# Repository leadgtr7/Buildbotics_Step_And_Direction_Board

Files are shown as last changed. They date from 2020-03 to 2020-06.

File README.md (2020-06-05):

Buildbotics Step and Direction Breakout and Level Shifter
======

### Intro
This is a step and direction breakout board and level shifter for the awesome Buildbotics CNC controller (https://buildbotics.com/ and https://github.com/buildbotics).

This board has been tested with the CL57Y closed loop stepper driver (https://www.omc-stepperonline.com/closed-loop-stepper-driver/y-series-closed-loop-stepper-driver-0-7-0a-24-50vdc-for-nema-17-23-24-stepper-motor.html).

I suspect that it will work with most drivers that have a minimum pulse width of 2.5uS even though the buildbotics control has a pulse width of 2 uS it just seems to work.

This board involves some small surface mount components (SOIC-8) so soldering skills are a must!

### You will need the following parts for the board

| Qty	| P/N	| Digikey Link |
| ---- | ---- | ---- |
|4x	|SN75451BDR	|https://www.digikey.com/product-detail/en/texas-instruments/SN75451BDR/296-14960-1-ND/562591|
|12x	|Generic Header Pins 2.54mm spacing	|https://www.amazon.com/MCIGICM-Header-2-45mm-Arduino-Connector/dp/B07PKKY8BX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|
|2x	|PCB-MB-01|https://www.digikey.com/product-detail/en/essentra-components/PCB-MB-01/RPC1760-ND/393158|
|4x |3 pin plugable terminal blocks 3.81mm spacing |https://www.amazon.com/gp/product/B07SVNGBZ7/ref=ppx_yo_dt_b_search_asin_title?ie=UTF8&psc=1|
|4x |0805 0.1uF Cap|https://www.digikey.com/product-detail/en/stackpole-electronics-inc/CML0805Y5V104ZT50V/738-CML0805Y5V104ZT50VCT-ND/10660252|

### Buildbotics PCB Modifications
You will need to solder in headers to the bbctrl board to make step and direction available as well as a 2 pin header with 5v and Ground. This will vary based on the version of your control board. You can find the schematics for the differnt revs here (https://github.com/buildbotics/bbctrl-pcb/tree/master/doc). For my controller (rev 8) you can see below for the locations.

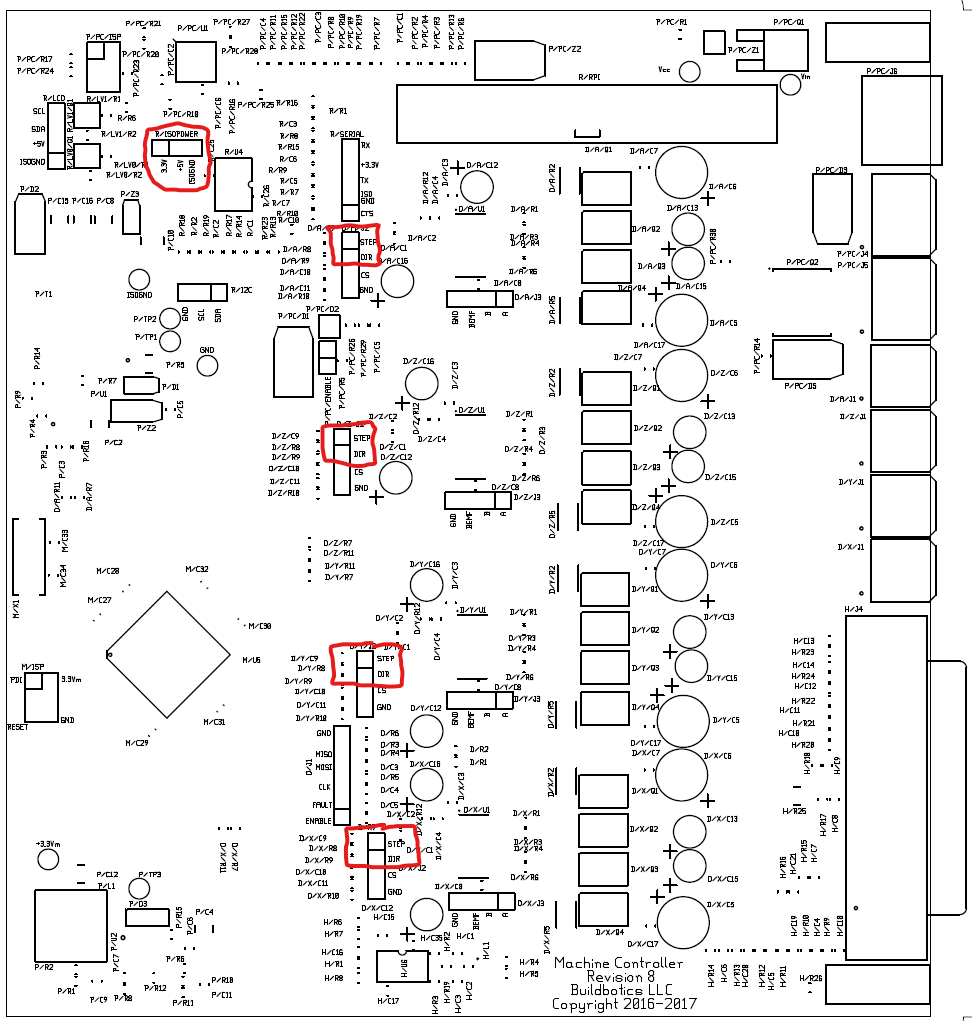
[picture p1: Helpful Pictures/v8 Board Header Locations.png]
v8 Header Locations


You will also need to make a harness to connect the 10 pins on the bbctrl to the step and direction board. If you aren't comfortable crimping your own harness you could use something like this (https://www.amazon.com/EDGELEC-Breadboard-Optional-Assorted-Multicolored/dp/B07GCY6CH7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) for your harness.

### PCB Assembly
The image below shows the location of all the headers and how to solder the ICs to the board. Each of the 3 pin connectors provides the step and direction output and the 4 sets of 2 pins are wired to the buildbotics pcb header you need to install. Remeber that as you plug in the cable on the back that they will be reversed on the front so pay attention to that.

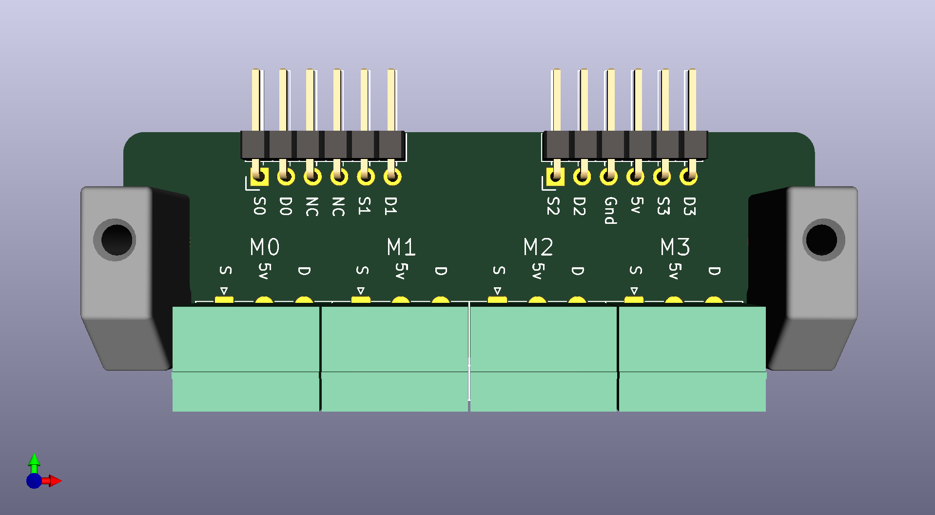
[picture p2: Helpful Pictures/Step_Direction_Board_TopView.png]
Front PCB


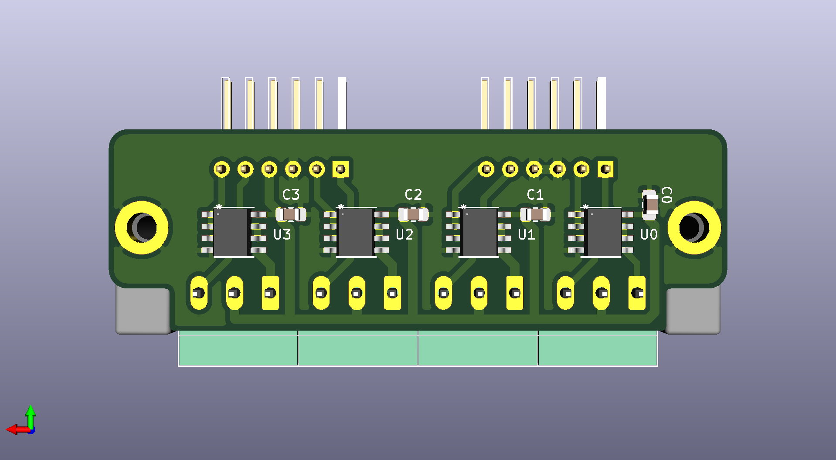
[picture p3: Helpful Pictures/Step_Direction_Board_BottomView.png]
Back PCB


note the direction of pin 1 of the IC's

### New Back Panel
The back of the buildbotics controller can be modified to accommodate the new board using the any of the files in the back panel folder. I use fusion 360 so i have included a fusion file with all of my tool paths and the like. You could also use the step file. 

I Used 1/16th in aluminum sheet to recreate the back piece (https://www.amazon.com/dp/B00HRHBB20/?coliid=IMIUESINE7ACL&colid=2XXWKYU69Q3UG&psc=1&ref_=lv_ov_lig_dp_it).

back panel

I think that about covers it. Thanks to Joe and Doug from buildbotics for an awesome product and helping me out in modifying the controller to suit my needs.

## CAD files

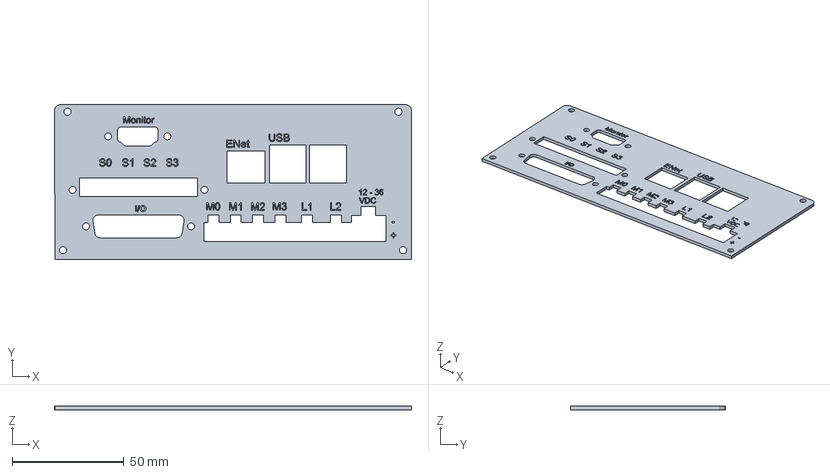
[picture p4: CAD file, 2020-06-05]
Back Plate 3D Files/bbctrl-back v8.step
159.7 x 69.2 x 1.59 mm

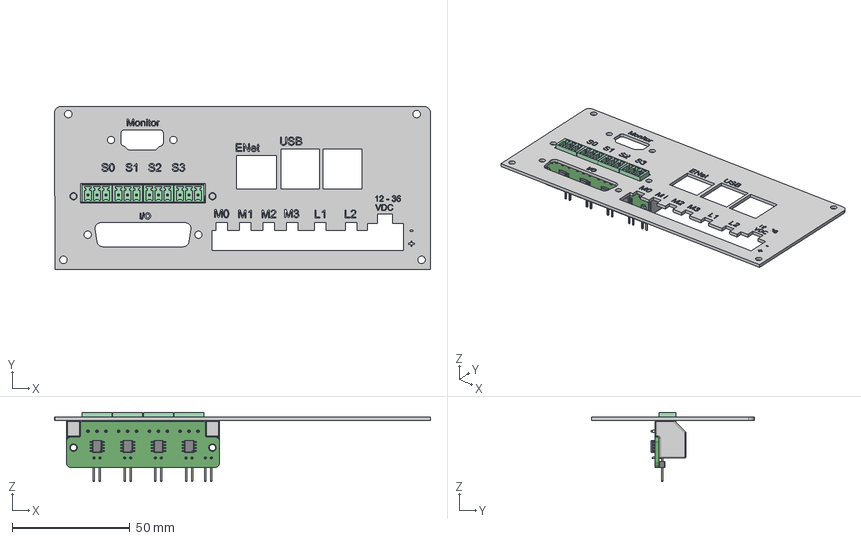
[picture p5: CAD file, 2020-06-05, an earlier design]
Back Plate 3D Files/bbctrl-back v7.step
159.7 x 69.2 x 29.4 mm
Back

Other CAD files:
Back Plate 3D Files/bbctrl-back v8.f3d
Back Plate 3D Files/bbctrl-back.f3z

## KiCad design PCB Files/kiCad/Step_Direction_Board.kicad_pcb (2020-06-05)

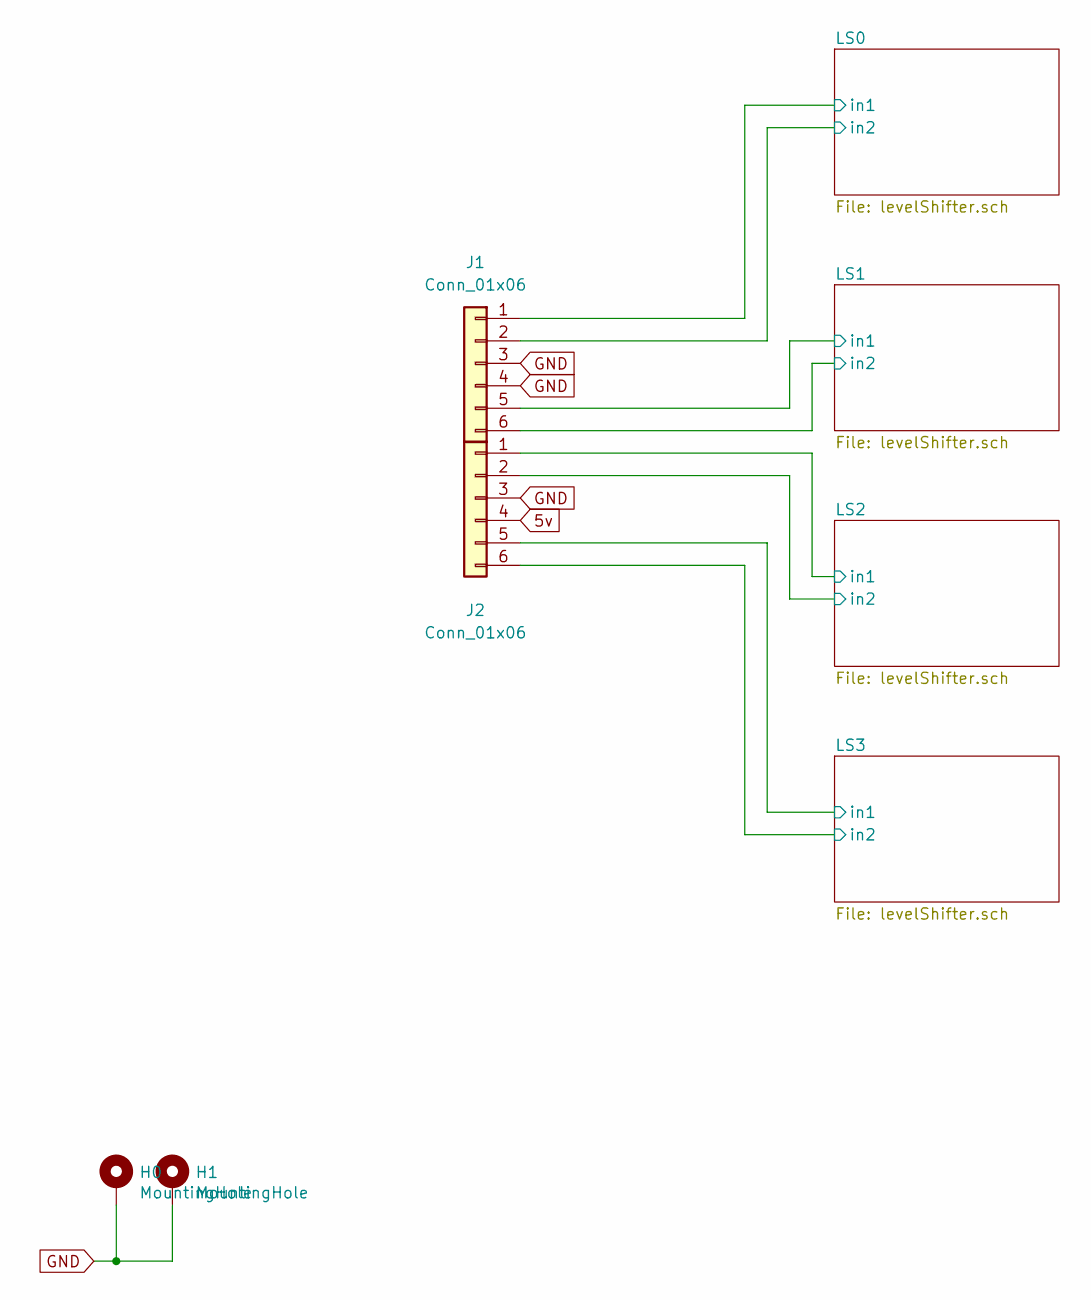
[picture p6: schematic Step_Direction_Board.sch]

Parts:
H0, H1: MountingHole; MountingHole_3.2mm_M3_ISO7380_Pad
J1, J2: Conn_01x06; PinHeader_1x06_P2.54mm_Horizontal

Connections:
5v: J2.4; also elsewhere on the board
/LS0/in1: J1.1; also elsewhere on the board
/LS0/in2: J1.2; also elsewhere on the board
/LS1/in1: J1.5; also elsewhere on the board
/LS1/in2: J1.6; also elsewhere on the board
/LS2/in1: J2.1; also elsewhere on the board
/LS2/in2: J2.2; also elsewhere on the board
/LS3/in1: J2.5; also elsewhere on the board
/LS3/in2: J2.6; also elsewhere on the board
GND: H0.1, H1.1, J1.3, J1.4, J2.3; also elsewhere on the board

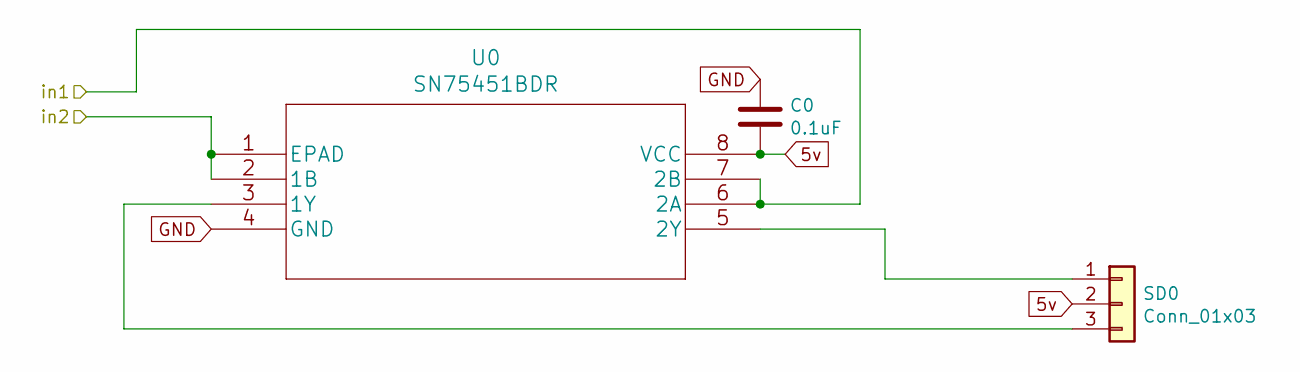
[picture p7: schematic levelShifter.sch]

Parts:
C0: 0.1uF; C_0805_2012Metric_Pad1.15x1.40mm_HandSolder
SD0: Conn_01x03; PhoenixContact_MC_1,5_3-G-3.81_1x03_P3.81mm_Horizontal
U0: SN75451BDR

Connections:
5v: C0.2, SD0.2, U0.8 (VCC); also elsewhere on the board
/LS0/in1: U0.6 (2A), U0.7 (2B); also elsewhere on the board
/LS0/in2: U0.1 (EPAD), U0.2 (1B); also elsewhere on the board
GND: C0.1, U0.4 (GND); also elsewhere on the board
unnamed: SD0.1, U0.5 (2Y)
unnamed: SD0.3, U0.3 (1Y)

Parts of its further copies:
C1, C2, C3: 0.1uF; C_0805_2012Metric_Pad1.15x1.40mm_HandSolder
SD1, SD2, SD3: Conn_01x03; PhoenixContact_MC_1,5_3-G-3.81_1x03_P3.81mm_Horizontal
U1, U2, U3: SN75451BDR

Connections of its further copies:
5v: C1.2, C2.2, C3.2, SD1.2, SD2.2, SD3.2, U1.8 (VCC), U2.8 (VCC), U3.8 (VCC); also elsewhere on the board
/LS1/in1: U1.6 (2A), U1.7 (2B); also elsewhere on the board
/LS1/in2: U1.1 (EPAD), U1.2 (1B); also elsewhere on the board
/LS2/in1: U2.6 (2A), U2.7 (2B); also elsewhere on the board
/LS2/in2: U2.1 (EPAD), U2.2 (1B); also elsewhere on the board
/LS3/in1: U3.6 (2A), U3.7 (2B); also elsewhere on the board
/LS3/in2: U3.1 (EPAD), U3.2 (1B); also elsewhere on the board
GND: C1.1, C2.1, C3.1, U1.4 (GND), U2.4 (GND), U3.4 (GND); also elsewhere on the board
unnamed: SD1.1, U1.5 (2Y)
unnamed: SD1.3, U1.3 (1Y)
unnamed: SD2.1, U2.5 (2Y)
unnamed: SD2.3, U2.3 (1Y)
unnamed: SD3.1, U3.5 (2Y)
unnamed: SD3.3, U3.3 (1Y)

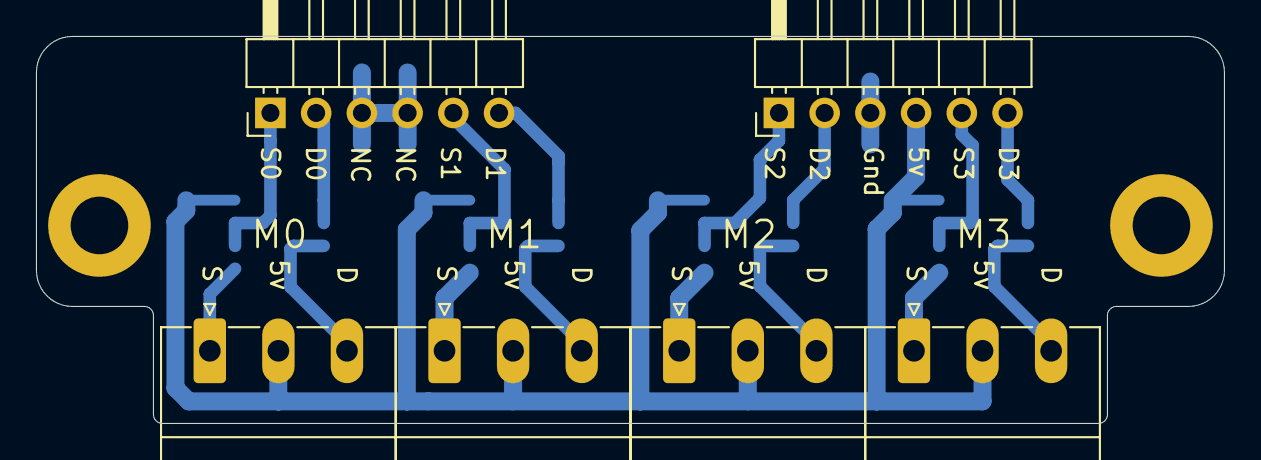
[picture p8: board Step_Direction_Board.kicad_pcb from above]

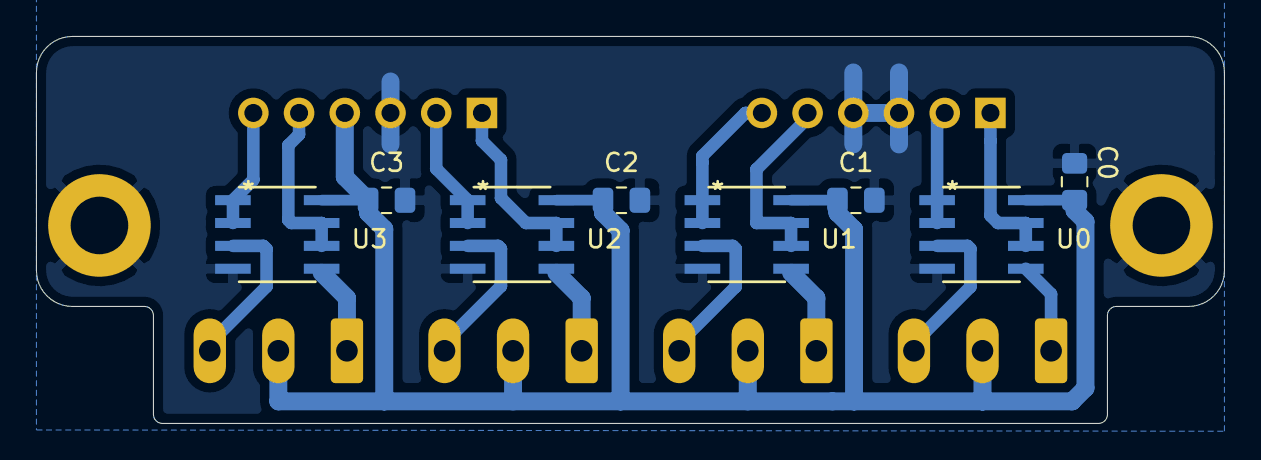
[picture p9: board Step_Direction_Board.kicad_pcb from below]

Board: 2 copper layers, 66.0 x 21.5 mm, 16 parts (8 on the bottom side), 18 nets.

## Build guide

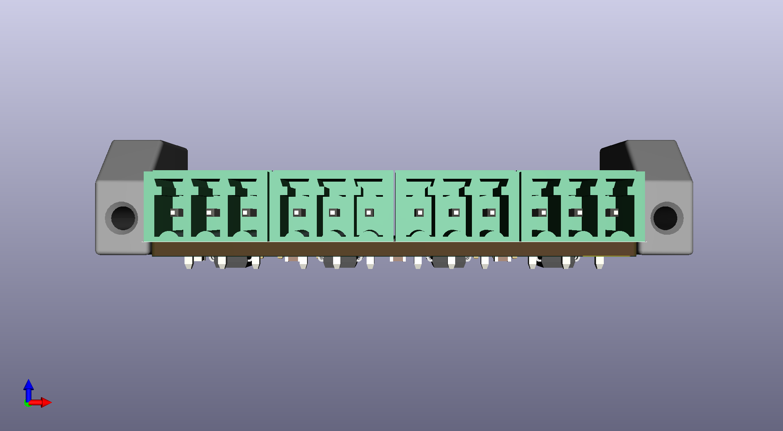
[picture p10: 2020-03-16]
Helpful Pictures/Step_Direction_Board_FrontView.png

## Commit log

2020-06-05 New And Updated Files
    [D8-L.step, D8-M.step, D8.step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]
2020-06-05 let's try this again
    [Step_Direction_Board-B_Cu.gbr, Step_Direction_Board-B_Mask.gbr, Step_Direction_Board-B_Paste.gbr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]

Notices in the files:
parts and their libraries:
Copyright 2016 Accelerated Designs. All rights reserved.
